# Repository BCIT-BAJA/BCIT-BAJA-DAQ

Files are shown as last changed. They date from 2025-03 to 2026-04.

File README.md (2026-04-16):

# Problem 
During the last BAJA competition,The BAJA team was unable to measure dynamic forces applied onto the suspension of the car. As a result, during the last competition, it bent.



The telemetry system for BCIT-BAJA car, collects strain across suspension components of car to allow BAJA to optimize material and reinforce weak areas of suspension.
As well as collect other data such as linear/angular acceleration.

There consists of 2 parts of this project. 

**PART B** the amplification of the (-15-15mV) analog strain signal to (0-3.0V) which is then routed to

**PART A**, which collects the 8 conditioned analog signals and is transmitted/received over a 915MHz antenna

# MAINBOARD( PART A)

Power supply circuitry


Conditioning of analog signals 


Additional peripherals used


# Amplifier circuit ( PART B) - 


Example of LTSPICE simulation used for amplifier board + signal conditioning



Verified amplifier board working


# Results of real-world appied force vs output voltage 


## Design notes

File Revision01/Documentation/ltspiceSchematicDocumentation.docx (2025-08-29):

# Power supply measurement

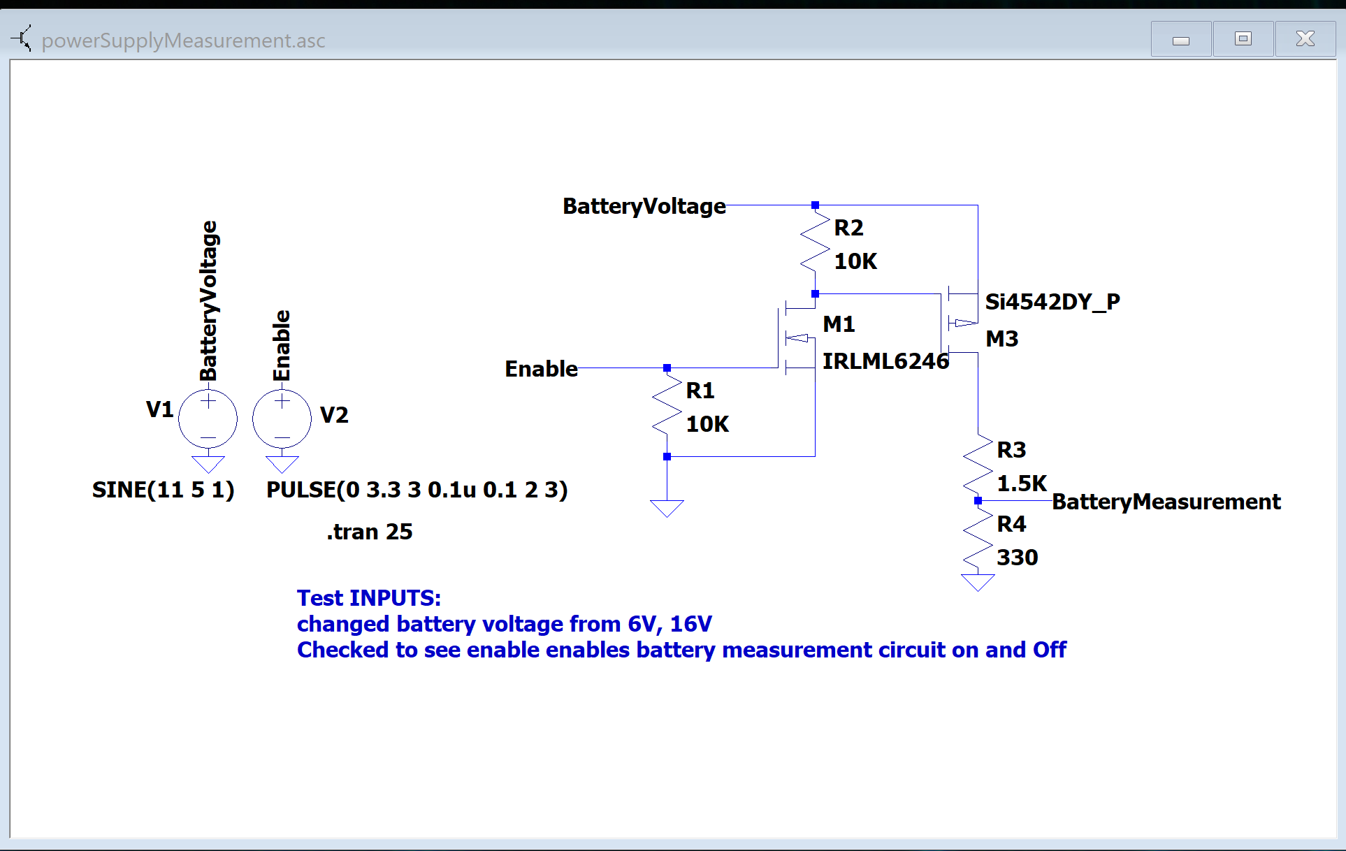
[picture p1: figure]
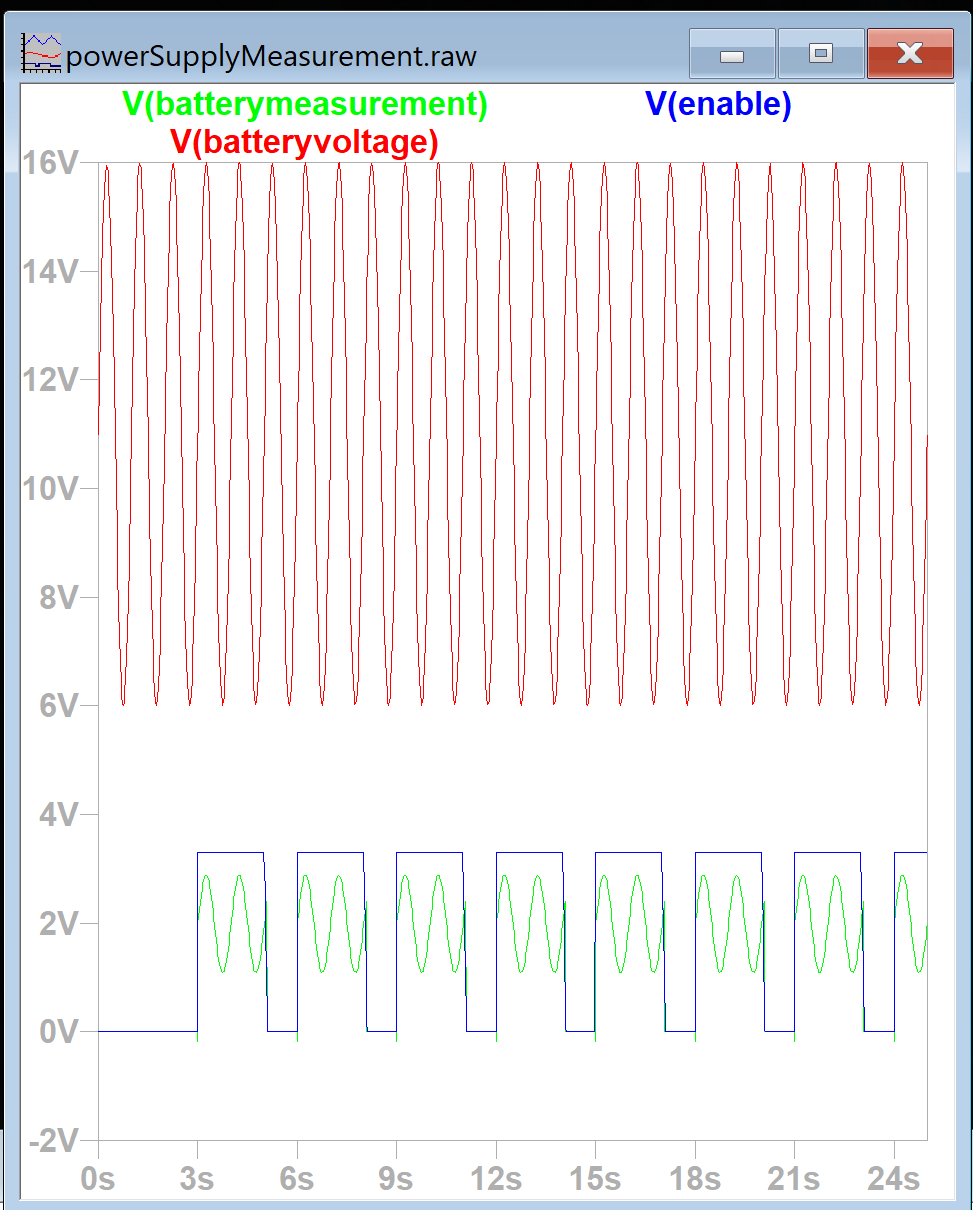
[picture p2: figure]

# StrainGAUGE switching

HIGH C -> LOW EMI, HIGH CURRENT DRAW, DECREASES ACCURACY

CURRENT LIMITING RESISTER -> LOWERS CURRENT, DECREASES ACCURACY

NO/VERY LOW C -> HIGHEST EMI, HIGHEST ACCURACY, lowest current draw.<-- chosen

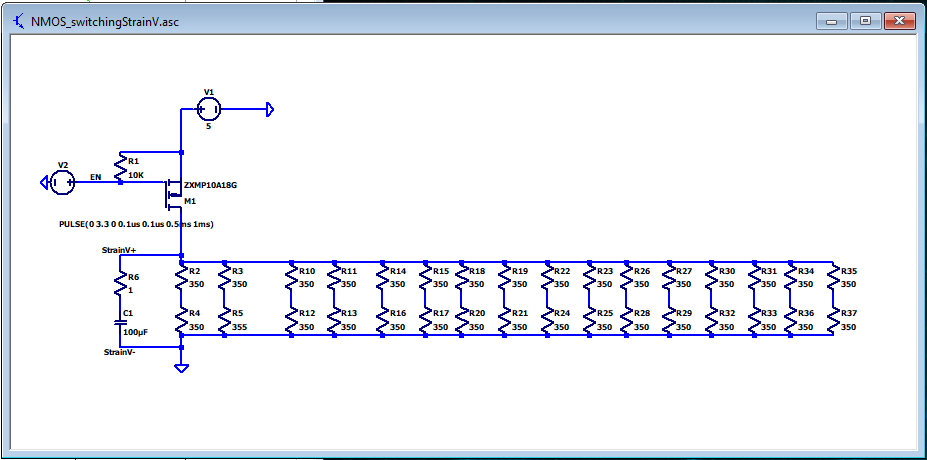
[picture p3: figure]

Figure 1 R =1Ω, C=100uF

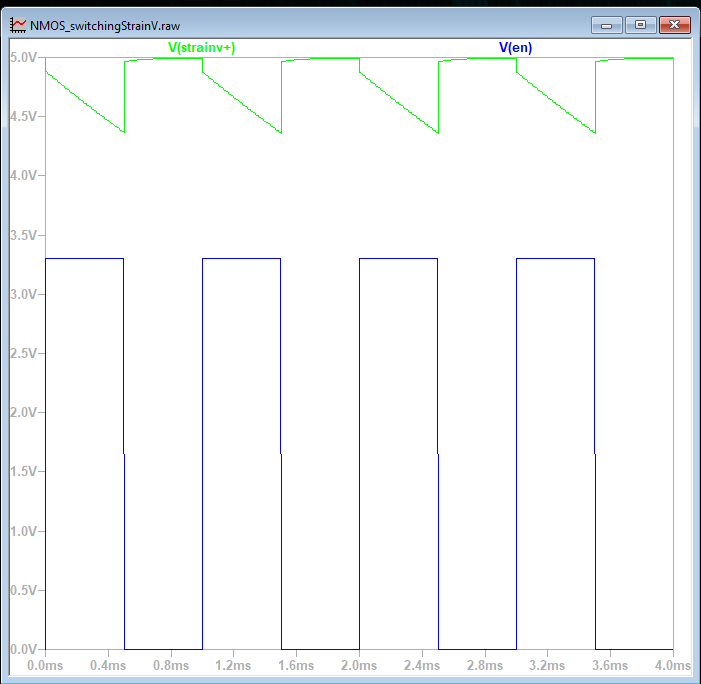
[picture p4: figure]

Figure 2 R =1Ω, C=100uF results

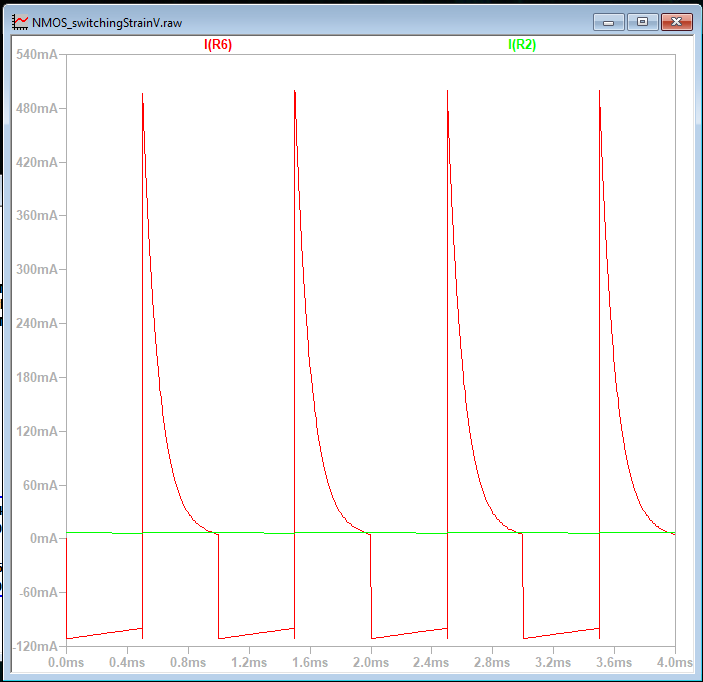
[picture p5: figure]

Figure 3 Current limiting resistor = 1 Ohm, bypass 100uF

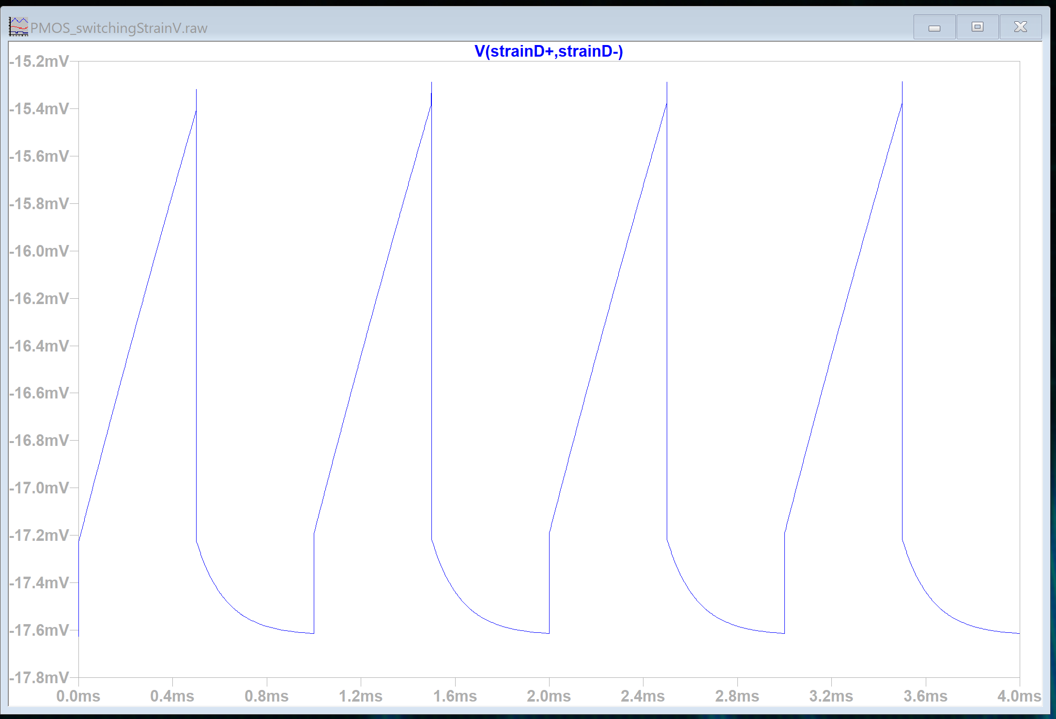
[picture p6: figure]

Figure 4 R =1, C=100uF

# Strain gauge Amplifier

Could not trigger undervoltage conditions on stimulation due to OP-AMP reaching saturation at about 500mV. The stimulated diodes are specced out for worst case condition. Triggering at -182mV, overall, the diodes still protect the ADC at worst-case scenario, however, could not be properly integrated into the stimulation.

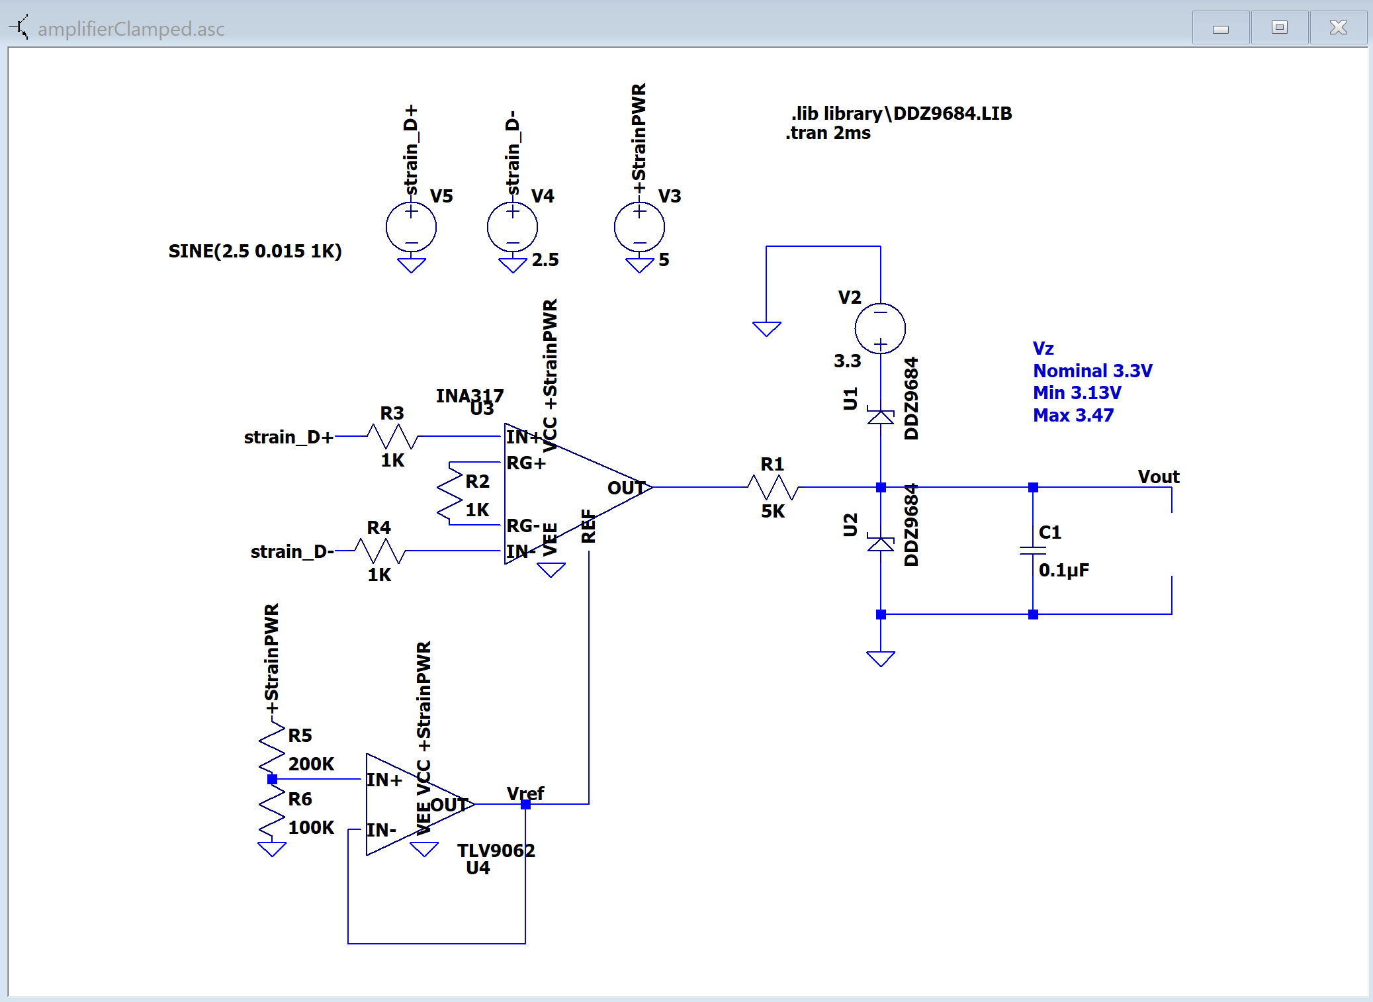
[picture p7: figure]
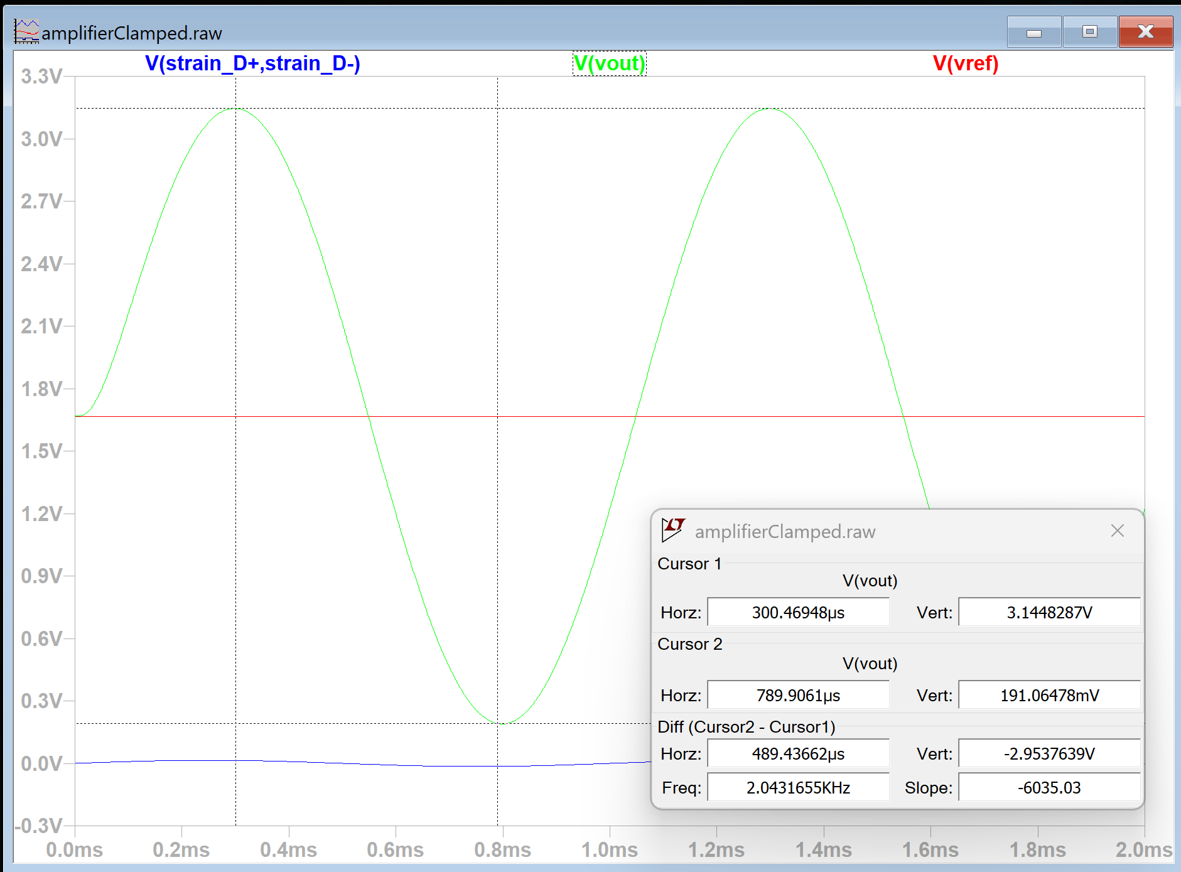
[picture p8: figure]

Diode clamping circuit (*Note, reverse voltage can vary quite a bit as seen by V_z in stimulation schematic)

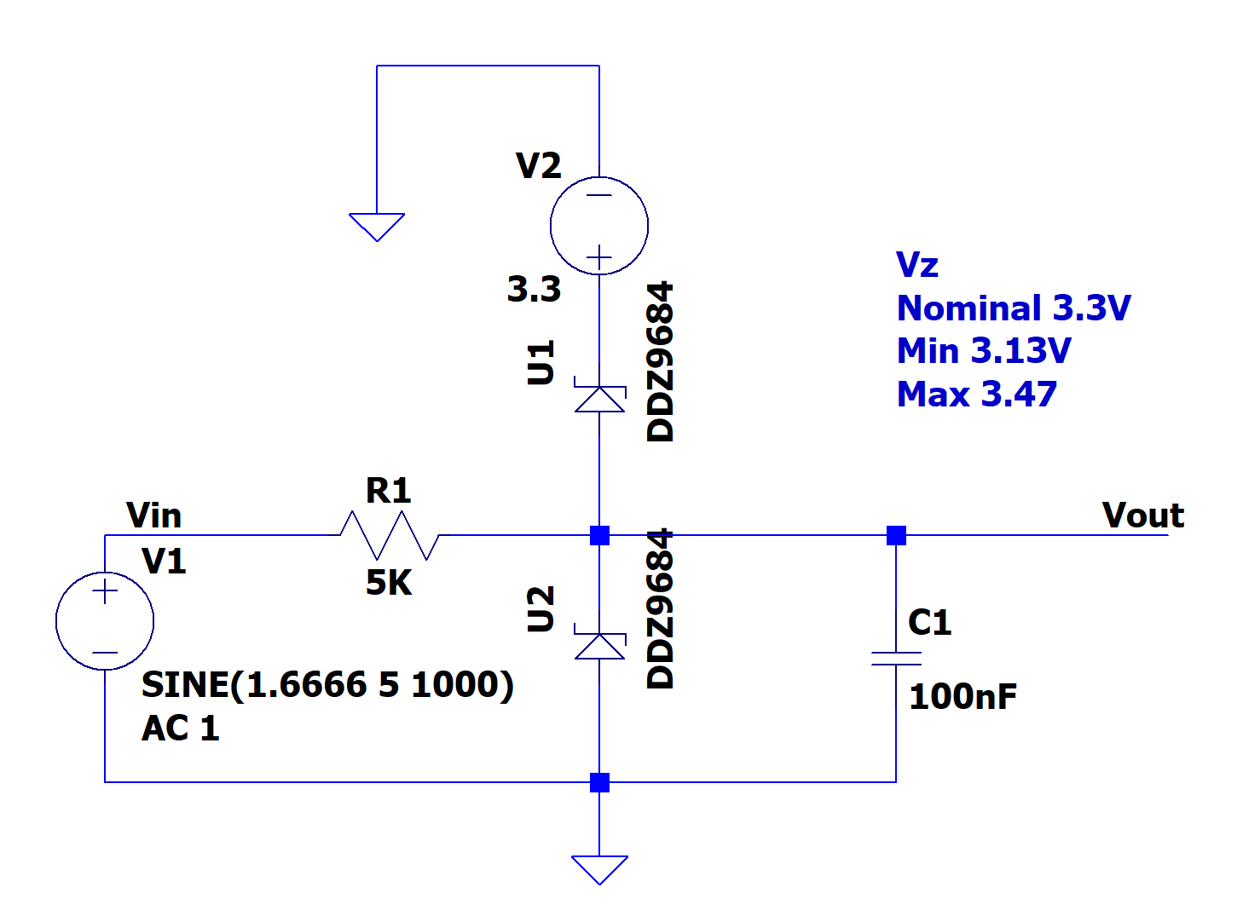
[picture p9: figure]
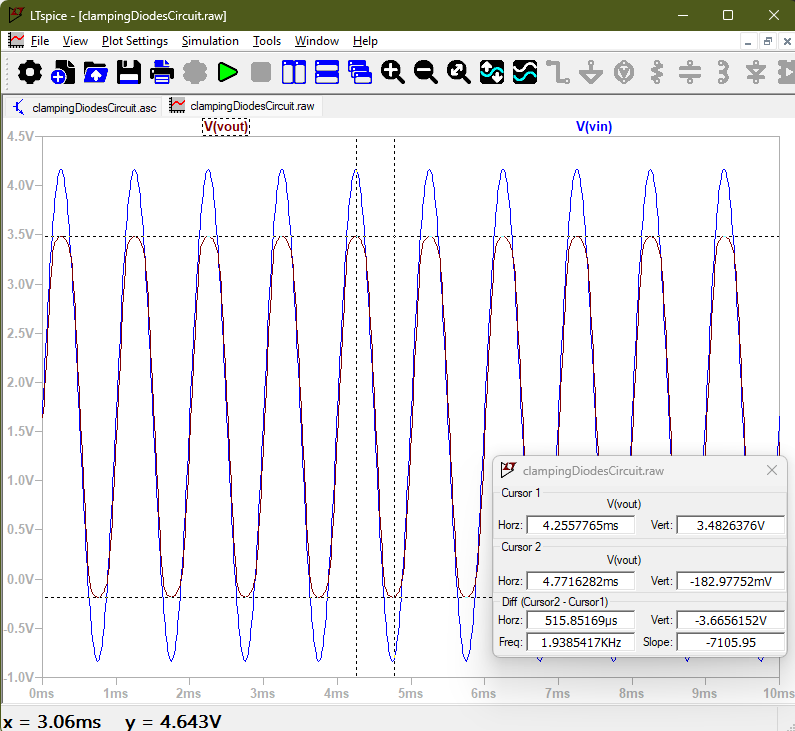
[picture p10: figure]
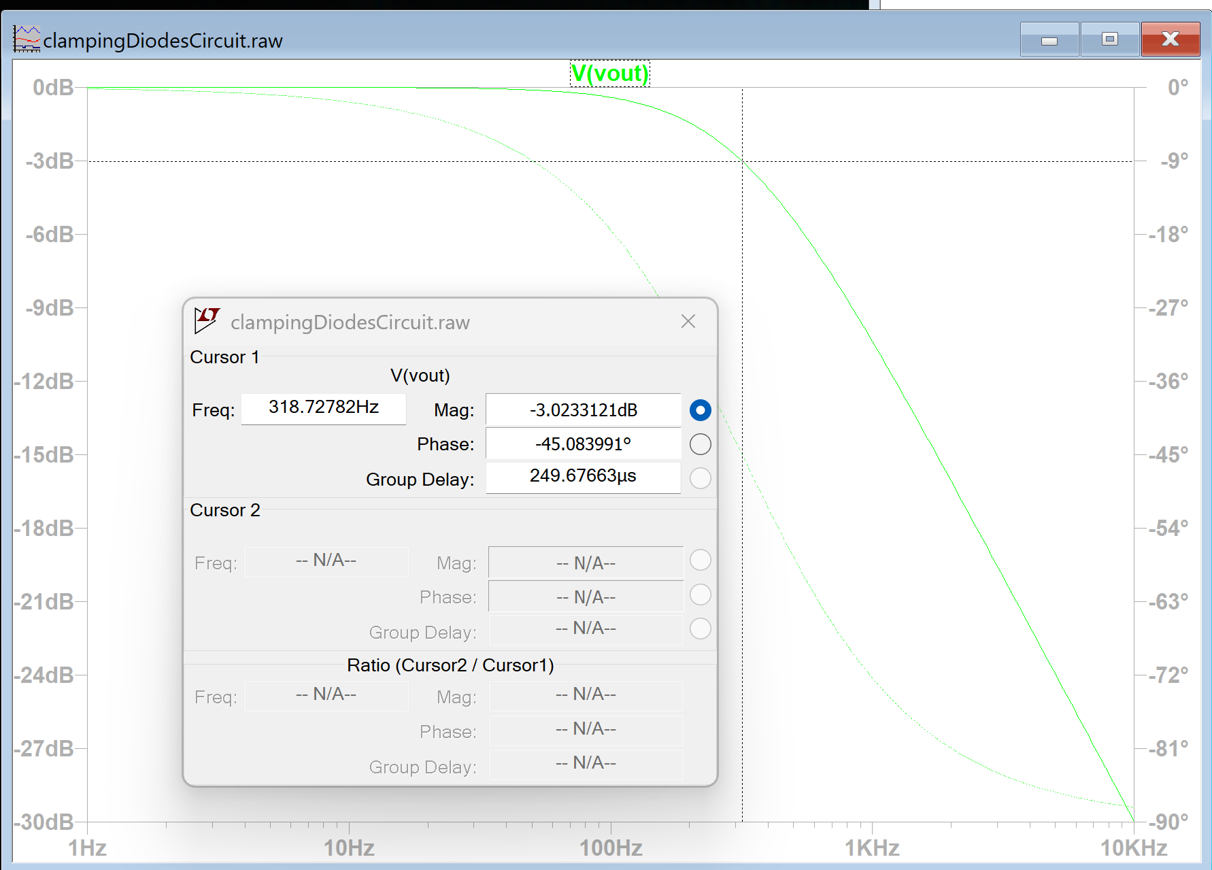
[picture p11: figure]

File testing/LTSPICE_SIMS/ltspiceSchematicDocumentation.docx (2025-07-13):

# Power supply measurement


# StrainGAUGE switching

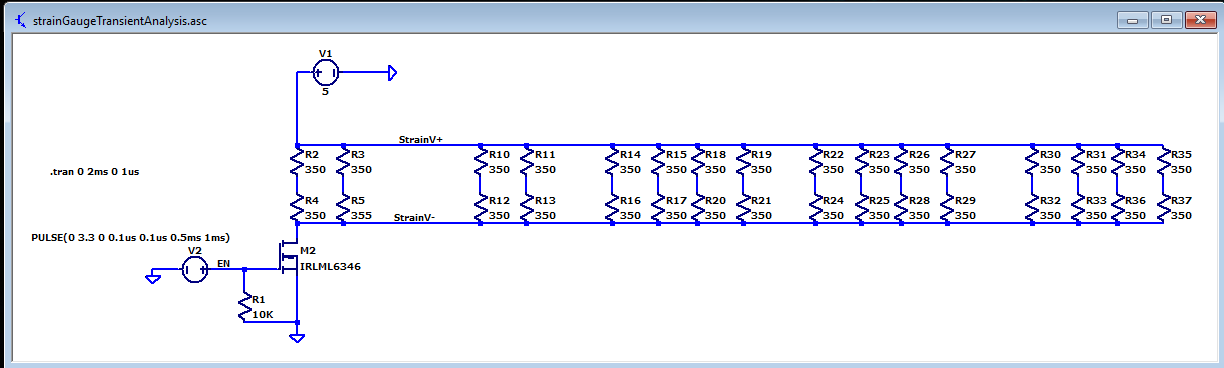
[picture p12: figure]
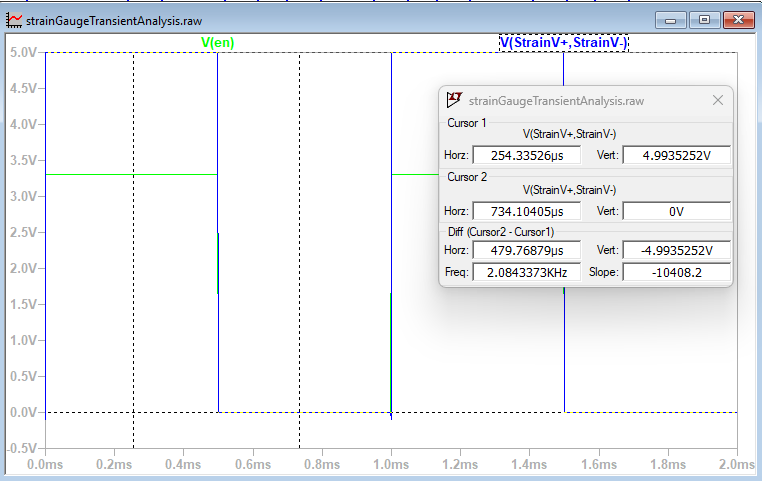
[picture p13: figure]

# Strain gauge Amplifier

I had difficulty combining with the clamping diodes in the next circuit. Wondering if it has to do with the output current of the OP-AMP. Will need to explore this a bit further.

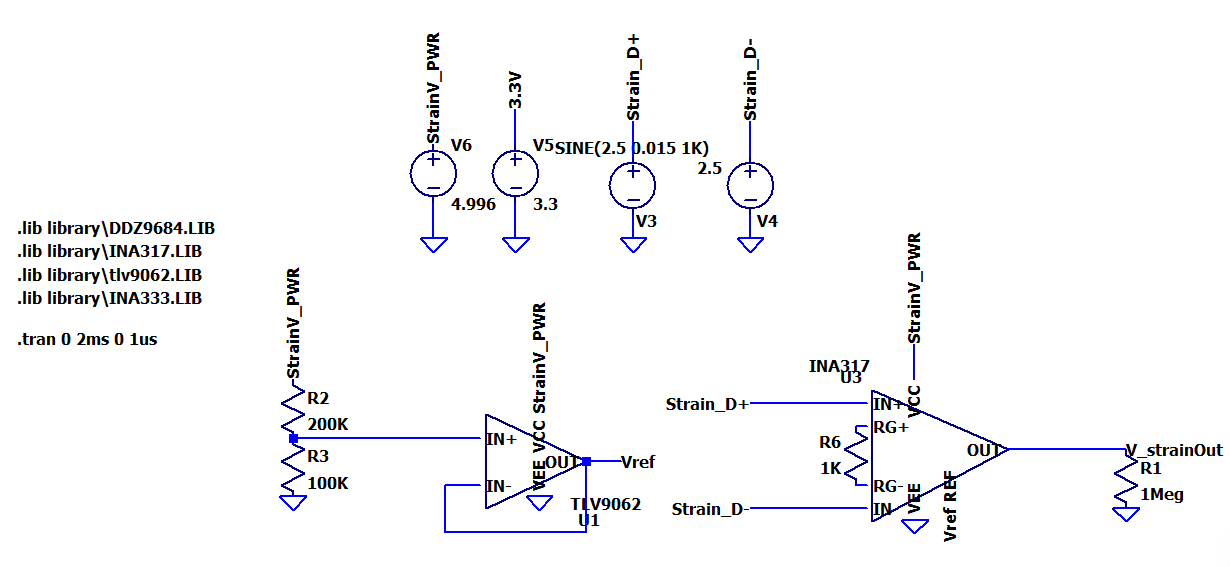
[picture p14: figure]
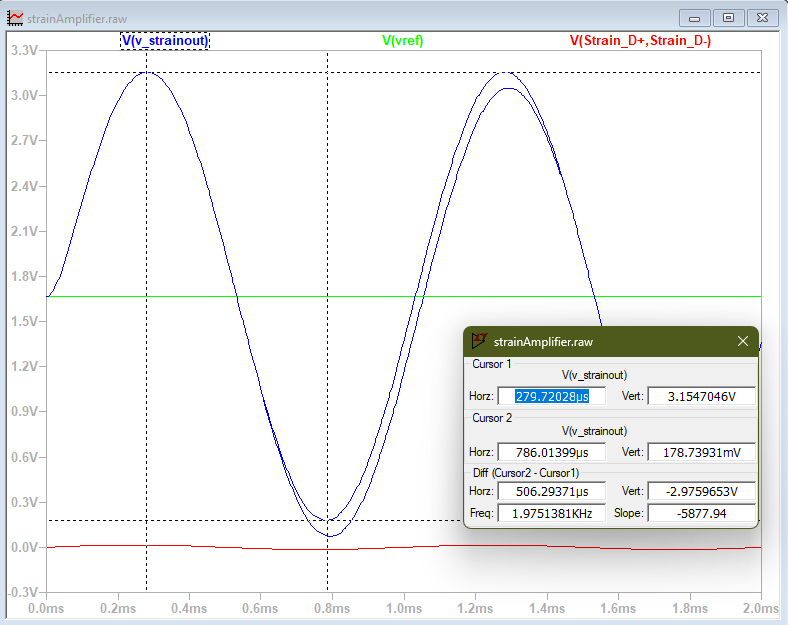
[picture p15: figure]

Diode clamping circuit(*Note, reverse voltage can vary quite a bit as seen by Vz on circuit)

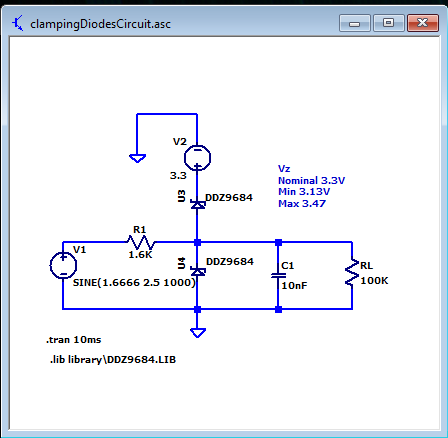
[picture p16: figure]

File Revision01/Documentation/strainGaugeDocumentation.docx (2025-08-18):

PMOS CALCULATIONS

NOTE: Calculations were performed assuming ALL strain gauges are connected. The resistance changes as strain Gauges are disconnected. Though it should be fine if we disconnect some.

For a PMOS

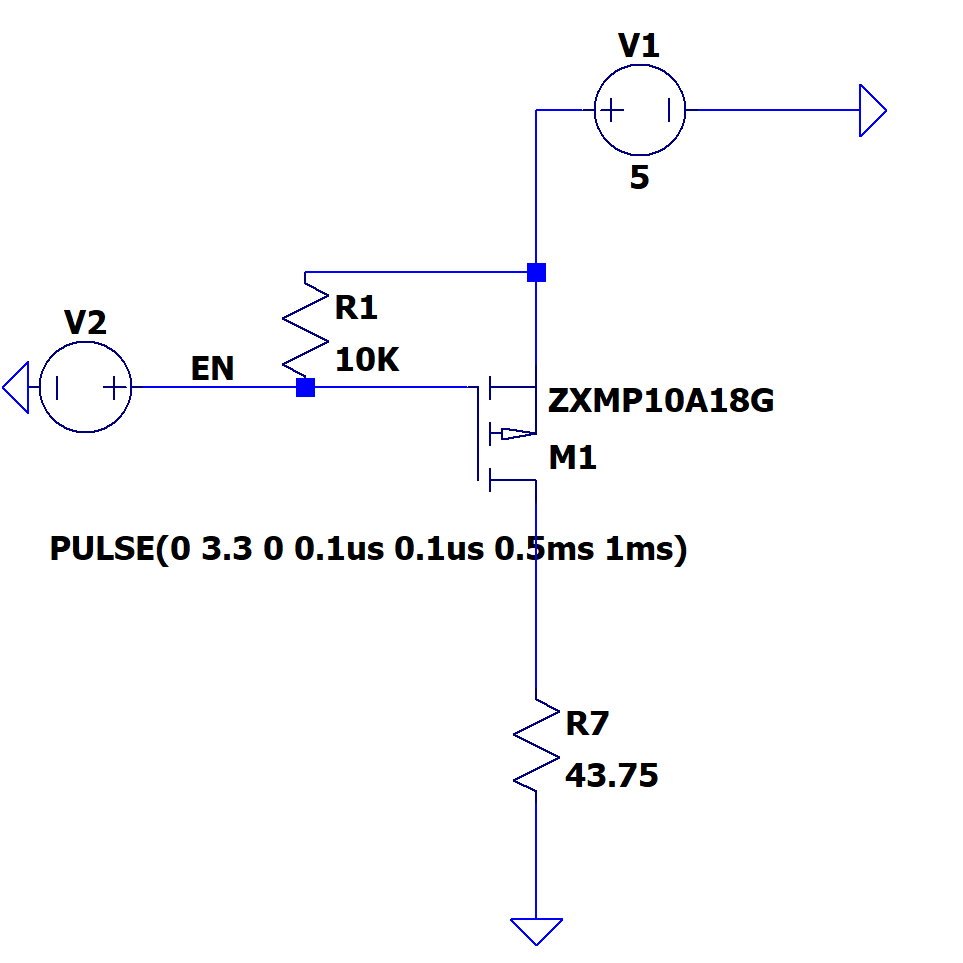
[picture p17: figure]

Figure 1 Similar model was run in stimulation, however not the same as what we choose

CUTOFF REGION: V_(sg) <V_(th_min)

5-3.3<2V

1.7<2V

YES IT can turn off

TRIODE REGION: (FULLY ON)

V_(sg) >V_(th_max)

5 > 4

V_(sd) <V_(sg) -|V_(th_max) |

ASSUME IN TRIODE REGION

Our V_(gs) =-5V when turned on so we can assume R_(ds) ≅1.5Ω

The unknown is V_d

i_d =(5V)/(1.5Ω+43.75Ω)=110mA

V_d =43.75*110mA=4.8125

V_(sd) =5-4.8125=0.1875V

V_(sd) <V_(sg) -|V_(th_max) |

0.1875<5-4

0.1875<1

Very ON!

# Bypass capacitor calculations as PMOS switches 1KHz. Check LTSPICE documentation for more indepth stimulation

I_load = 114mA

Delta T = 0.5ms

Delta V = 0.5V <- just setting it as such

I = C dV/dT

C = I * dT/dV

C = 114mA * 0.5ms / 0.5

= 114 uF ~= 100uF

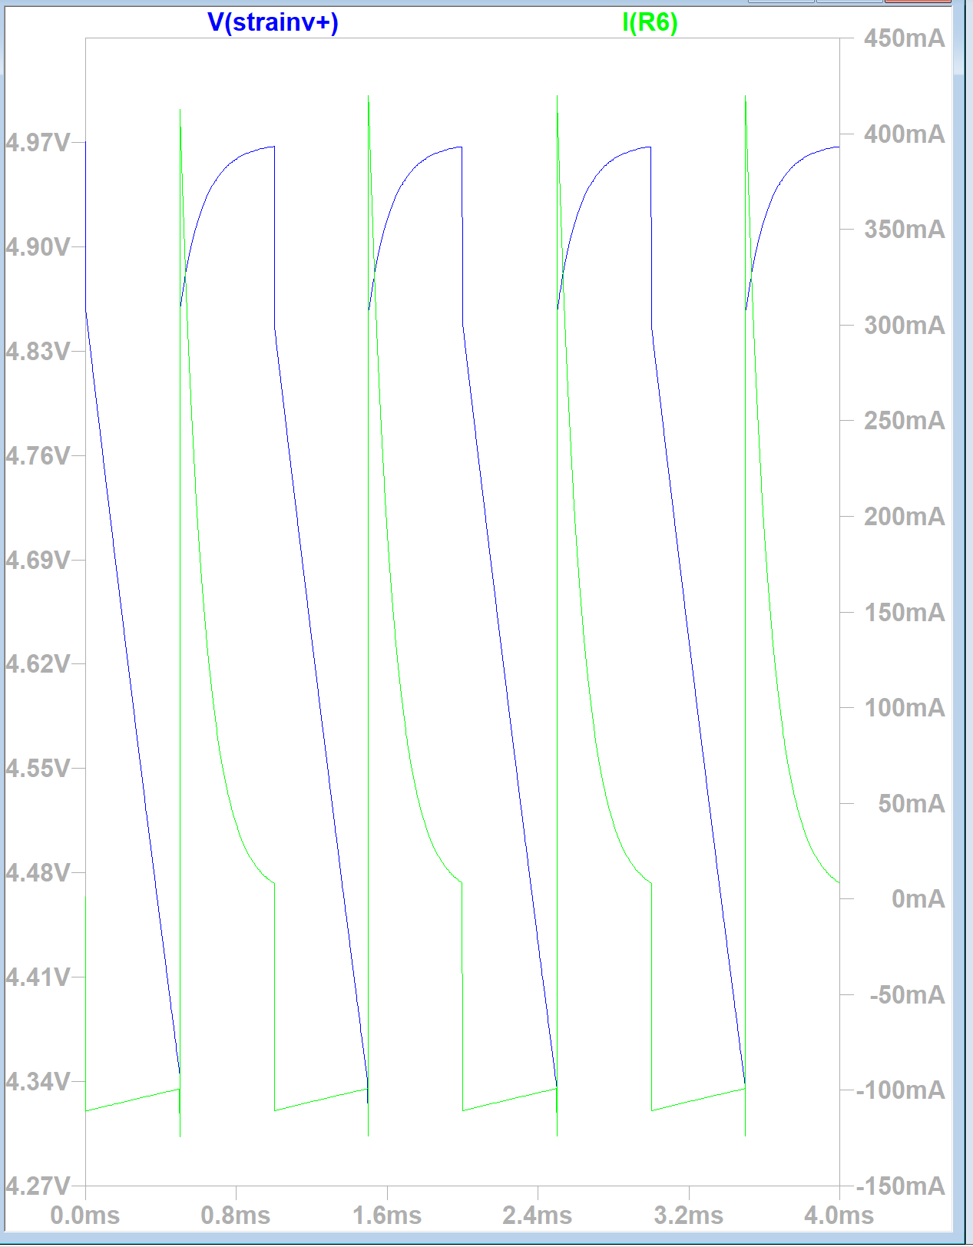
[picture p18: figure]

Figure 2 Assuming C=100uF, ended up not using due to high spike in current

# What happens to differential strain analog signal as 5V rail changes?

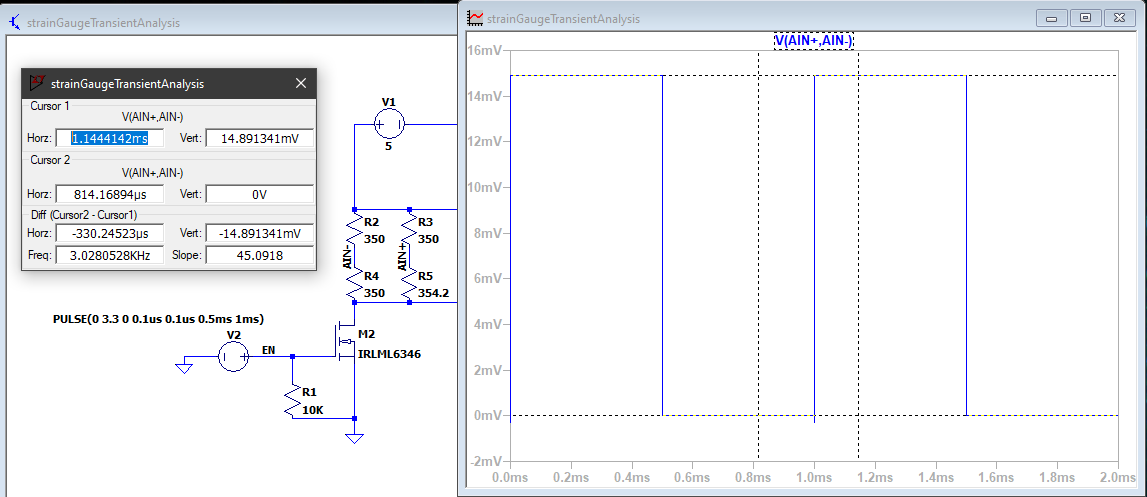
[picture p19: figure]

Figure 3 : 5V rail = 5V, differential signal = 14.89mV

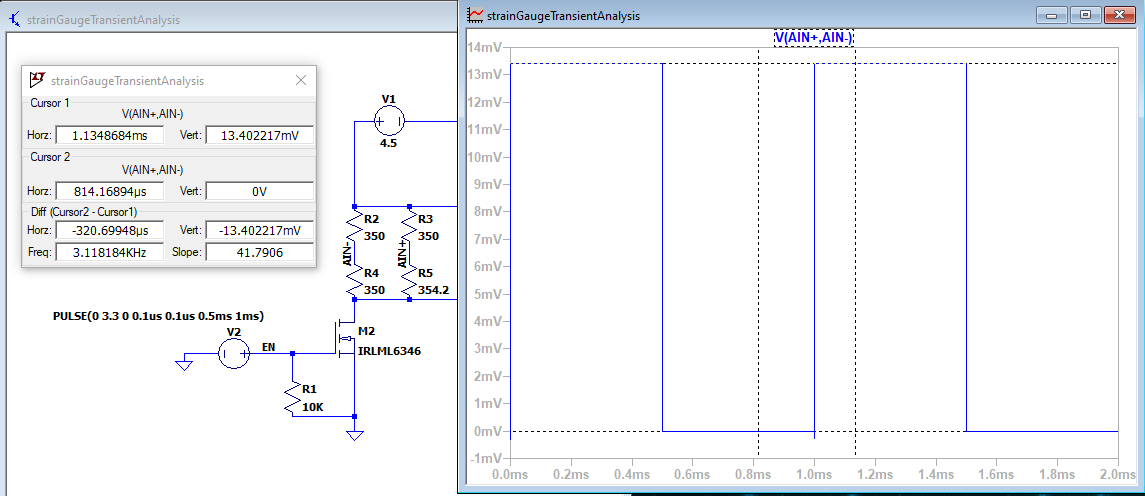
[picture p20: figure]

Figure 4 : 5V rail = 4.5V, differential signal =13.47mV

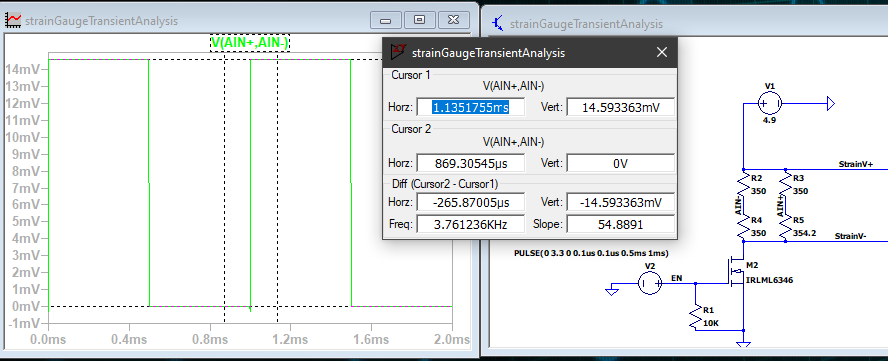
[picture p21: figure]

Figure 5 : 5V rail = 4.9, differential signal =14.59mV

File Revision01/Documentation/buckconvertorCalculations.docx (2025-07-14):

Specifications

1. Verification of PINOUT

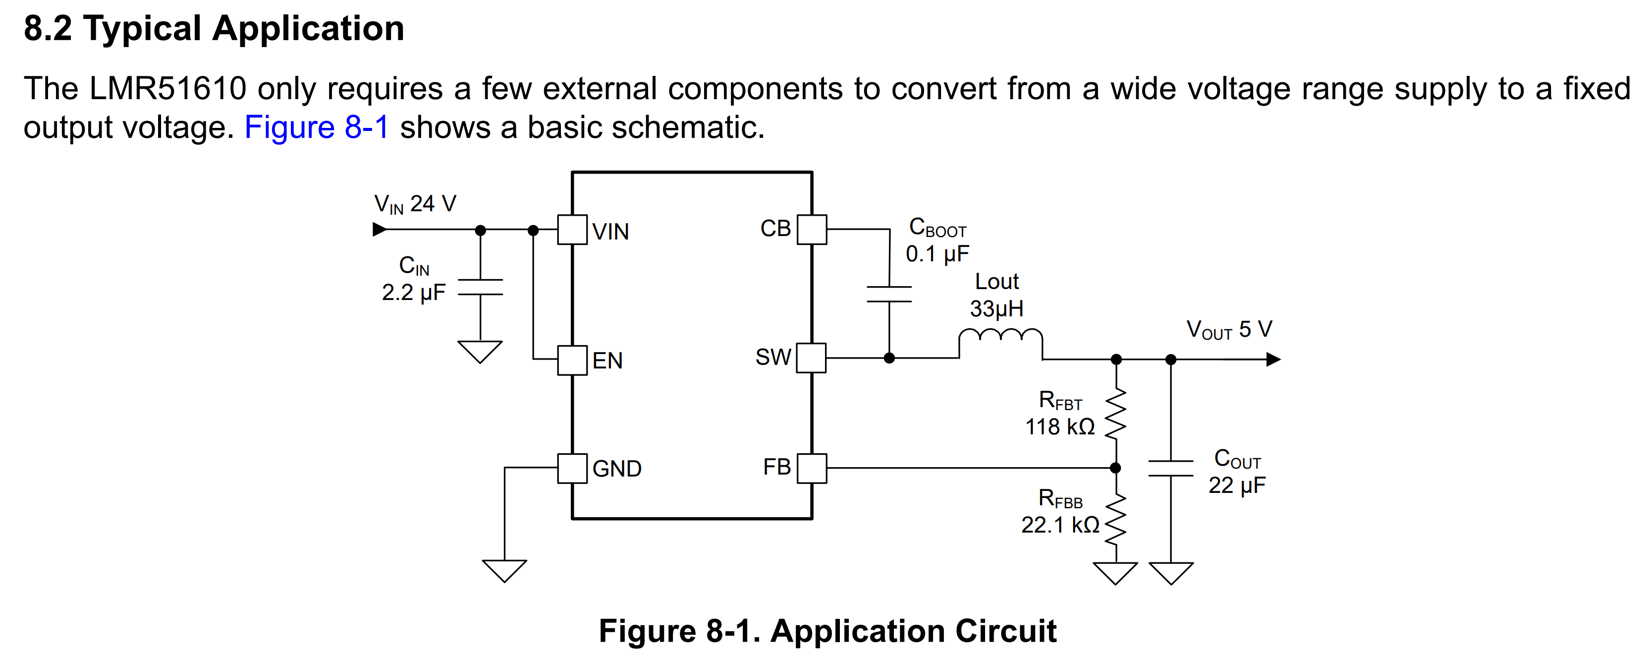
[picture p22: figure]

Design parameters

Parameter | Value
V_(in) | 4.5-16V - Not sure why (8.8V - 15.2V) is on schematic
V_(out) | 7V – must be above 6.5V
i_(out_max) | 250mA – (assuming MOSFET is not switched at 1KHz)
Output overshoot, undershoot | ±5%
Output voltage ripple | ±5%
Operating frequency | 400KHz

2. How do you set the output voltage? (PRIORITY HIGH)

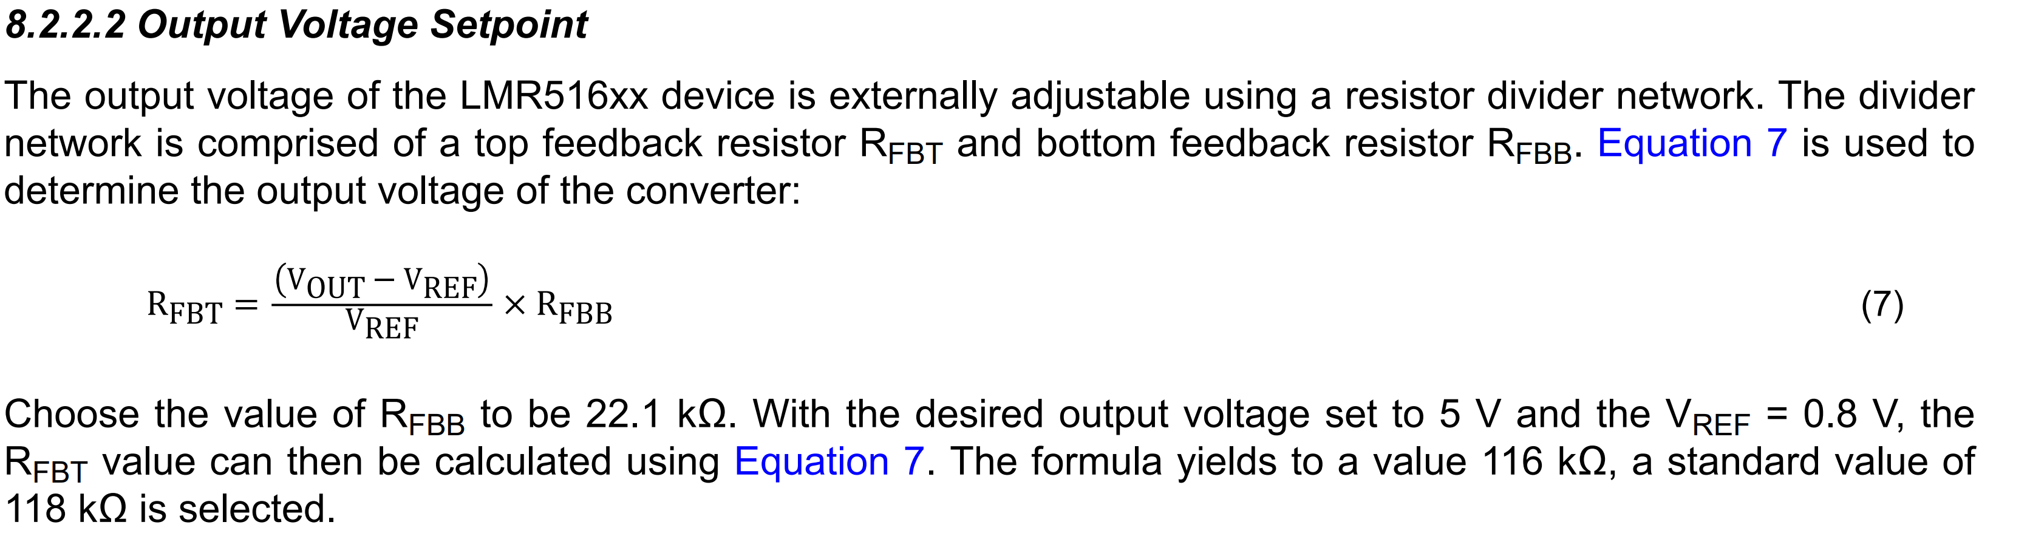
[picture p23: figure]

Defining variables

Choose V_(out) = 7V (Ensure V_(out) is above 6.5V for stable operation of LDO)

V_(ref) = 0.8V (Const)

R_(fbb) = 10K (Randomly chosen)

Plugging that into eq we get

R_(fbt) = (V_(out) - V_(ref) )*(R_(fbb))/(V_(ref))= 77.5K ~= 76.8K

3. How to choose output inductor (PRIORITY MEDIUM)

Overall, I chose parameters that limited EMI, at the cost of being less energy efficient.

K_(IND) is a coefficient that represents the amount of inductor ripple current relative to the maximum output current of the device. K_(IND) must be 0.2-0.6 of maximum IOUT supported by converter.

K_(chosen) = 0.2 – lowest EMI, least energy efficient

f_(sw) =400KHz - lower switching frequency variant chosen for less EMI

V_(in_max) =16V - not sure why 15.2V was chosen

V_(out) =7V±0.5V

I_(out_fla) ~=250mA

Plugging the old parameters in we get

Figure 1 Formula used for inductance

L_(min) =197μH

We chose L =150μH giving us K = 0.26

Now we can calculate the ripple across the input of the inductor using

Figure 2 ripple current(PG 19 datasheet)

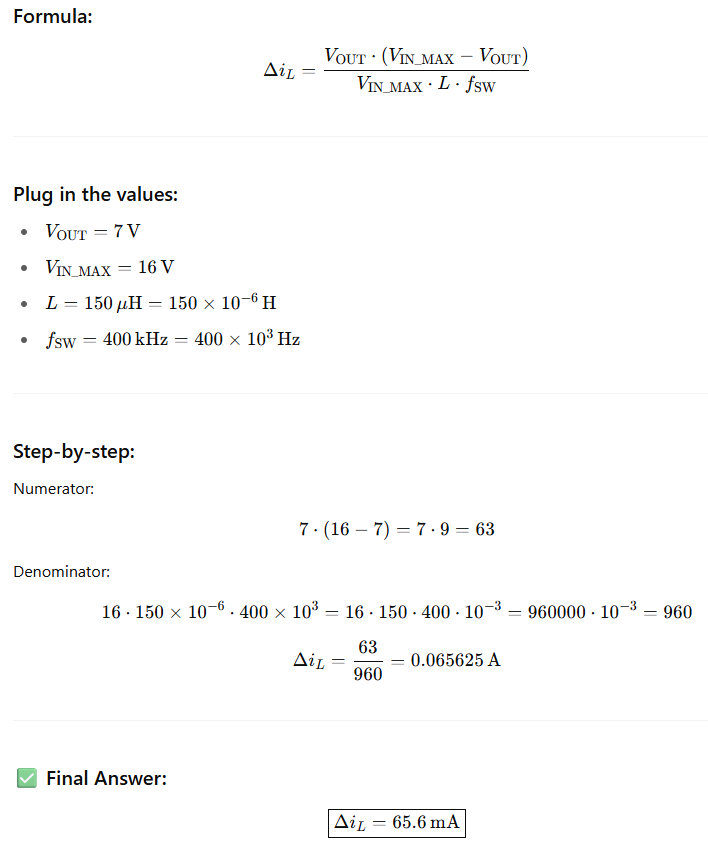
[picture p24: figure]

Note* This inductor has been routed away from analog signals to reduce EMI.

4. Choosing Input capacitors (PRIORITY: LOW)

Followed recommendation using 1uF

5. Choosing output capacitor( PRIORITY: LOWish)

Target ripple is 0.35V

ESR ~= 10m Ω @300KHz

ΔV_(out_esr) =0.66mV

ΔV_(out) _c = 0.93mV


I will have 10uF + 1uF

This one may be better as all wiring has already been created.

Export TPS54202DDCR - 8.5V-16V to 7.00V @ 0.3A

https://webench.ti.com/power-designer/switching-regulator/select

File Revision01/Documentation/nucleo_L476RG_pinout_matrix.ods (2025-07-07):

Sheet: tabula-stm32l476rg(2)
AF15 | Pin | Additional Functions | AF0 | AF1 | AF2 | AF3 | AF4 | AF5 | AF6 | AF7 | AF8 | AF9 | AF10 | AF11 | AF12 | AF13 | AF14 | Pin | Additional Functions | AF0 | AF1 | AF2 | AF3 | AF4 | AF5 | AF6 | AF7 | AF8 | AF9 | AF10 | AF11 | AF12 | AF13 | AF14 | 0
EVENTOUT | PA0 | OPAMP1_VINP/ADC12_IN5/RTC_TAMP2/WKUP1 |  | TIM2_CH1 | TIM5_CH1 | TIM8_ETR |  |  |  | USART2_CTS | UART4_TX |  |  |  |  | SAI1_EXTCLK | TIM2_ETR | PA0 | PA0/OPAMP1_VINP/ADC12_IN5/RTC_TAMP2/WKUP1 | PA0/OPAMP1_VINP/ADC12_IN5/RTC_TAMP2/WKUP1 | PA0/OPAMP1_VINP/ADC12_IN5/RTC_TAMP2/WKUP1/TIM2_CH1 | PA0/OPAMP1_VINP/ADC12_IN5/RTC_TAMP2/WKUP1/TIM2_CH1/TIM5_CH1 | PA0/OPAMP1_VINP/ADC12_IN5/RTC_TAMP2/WKUP1/TIM2_CH1/TIM5_CH1/TIM8_ETR | PA0/OPAMP1_VINP/ADC12_IN5/RTC_TAMP2/WKUP1/TIM2_CH1/TIM5_CH1/TIM8_ETR | PA0/OPAMP1_VINP/ADC12_IN5/RTC_TAMP2/WKUP1/TIM2_CH1/TIM5_CH1/TIM8_ETR | PA0/OPAMP1_VINP/ADC12_IN5/RTC_TAMP2/WKUP1/TIM2_CH1/TIM5_CH1/TIM8_ETR | PA0/OPAMP1_VINP/ADC12_IN5/RTC_TAMP2/WKUP1/TIM2_CH1/TIM5_CH1/TIM8_ETR/USART2_CTS | PA0/OPAMP1_VINP/ADC12_IN5/RTC_TAMP2/WKUP1/TIM2_CH1/TIM5_CH1/TIM8_ETR/USART2_CTS/UART4_TX | PA0/OPAMP1_VINP/ADC12_IN5/RTC_TAMP2/WKUP1/TIM2_CH1/TIM5_CH1/TIM8_ETR/USART2_CTS/UART4_TX | PA0/OPAMP1_VINP/ADC12_IN5/RTC_TAMP2/WKUP1/TIM2_CH1/TIM5_CH1/TIM8_ETR/USART2_CTS/UART4_TX | PA0/OPAMP1_VINP/ADC12_IN5/RTC_TAMP2/WKUP1/TIM2_CH1/TIM5_CH1/TIM8_ETR/USART2_CTS/UART4_TX | PA0/OPAMP1_VINP/ADC12_IN5/RTC_TAMP2/WKUP1/TIM2_CH1/TIM5_CH1/TIM8_ETR/USART2_CTS/UART4_TX | PA0/OPAMP1_VINP/ADC12_IN5/RTC_TAMP2/WKUP1/TIM2_CH1/TIM5_CH1/TIM8_ETR/USART2_CTS/UART4_TX/SAI1_EXTCLK | PA0/OPAMP1_VINP/ADC12_IN5/RTC_TAMP2/WKUP1/TIM2_CH1/TIM5_CH1/TIM8_ETR/USART2_CTS/UART4_TX/SAI1_EXTCLK/TIM2_ETR | PA0/OPAMP1_VINP/ADC12_IN5/RTC_TAMP2/WKUP1/TIM2_CH1/TIM5_CH1/TIM8_ETR/USART2_CTS/UART4_TX/SAI1_EXTCLK/TIM2_ETR
EVENTOUT | PA1 | OPAMP1_VINM/ADC12_IN6 |  | TIM2_CH2 | TIM5_CH2 |  |  |  |  | USART2_RTS_DE | UART4_RX |  |  | LCD_SEG0 |  |  | TIM15_CH1N | PA1 | PA1/OPAMP1_VINM/ADC12_IN6 | PA1/OPAMP1_VINM/ADC12_IN6 | PA1/OPAMP1_VINM/ADC12_IN6/TIM2_CH2 | PA1/OPAMP1_VINM/ADC12_IN6/TIM2_CH2/TIM5_CH2 | PA1/OPAMP1_VINM/ADC12_IN6/TIM2_CH2/TIM5_CH2 | PA1/OPAMP1_VINM/ADC12_IN6/TIM2_CH2/TIM5_CH2 | PA1/OPAMP1_VINM/ADC12_IN6/TIM2_CH2/TIM5_CH2 | PA1/OPAMP1_VINM/ADC12_IN6/TIM2_CH2/TIM5_CH2 | PA1/OPAMP1_VINM/ADC12_IN6/TIM2_CH2/TIM5_CH2/USART2_RTS_DE | PA1/OPAMP1_VINM/ADC12_IN6/TIM2_CH2/TIM5_CH2/USART2_RTS_DE/UART4_RX | PA1/OPAMP1_VINM/ADC12_IN6/TIM2_CH2/TIM5_CH2/USART2_RTS_DE/UART4_RX | PA1/OPAMP1_VINM/ADC12_IN6/TIM2_CH2/TIM5_CH2/USART2_RTS_DE/UART4_RX | PA1/OPAMP1_VINM/ADC12_IN6/TIM2_CH2/TIM5_CH2/USART2_RTS_DE/UART4_RX/LCD_SEG0 | PA1/OPAMP1_VINM/ADC12_IN6/TIM2_CH2/TIM5_CH2/USART2_RTS_DE/UART4_RX/LCD_SEG0 | PA1/OPAMP1_VINM/ADC12_IN6/TIM2_CH2/TIM5_CH2/USART2_RTS_DE/UART4_RX/LCD_SEG0 | PA1/OPAMP1_VINM/ADC12_IN6/TIM2_CH2/TIM5_CH2/USART2_RTS_DE/UART4_RX/LCD_SEG0/TIM15_CH1N | PA1/OPAMP1_VINM/ADC12_IN6/TIM2_CH2/TIM5_CH2/USART2_RTS_DE/UART4_RX/LCD_SEG0/TIM15_CH1N
EVENTOUT | PA2 | ADC12_IN7/WKUP4/LSCO |  | TIM2_CH3 | TIM5_CH3 |  |  |  |  | USART2_TX |  |  |  | LCD_SEG1 |  | SAI2_EXTCLK | TIM15_CH1 | PA2 | PA2/ADC12_IN7/WKUP4/LSCO | PA2/ADC12_IN7/WKUP4/LSCO | PA2/ADC12_IN7/WKUP4/LSCO/TIM2_CH3 | PA2/ADC12_IN7/WKUP4/LSCO/TIM2_CH3/TIM5_CH3 | PA2/ADC12_IN7/WKUP4/LSCO/TIM2_CH3/TIM5_CH3 | PA2/ADC12_IN7/WKUP4/LSCO/TIM2_CH3/TIM5_CH3 | PA2/ADC12_IN7/WKUP4/LSCO/TIM2_CH3/TIM5_CH3 | PA2/ADC12_IN7/WKUP4/LSCO/TIM2_CH3/TIM5_CH3 | PA2/ADC12_IN7/WKUP4/LSCO/TIM2_CH3/TIM5_CH3/USART2_TX | PA2/ADC12_IN7/WKUP4/LSCO/TIM2_CH3/TIM5_CH3/USART2_TX | PA2/ADC12_IN7/WKUP4/LSCO/TIM2_CH3/TIM5_CH3/USART2_TX | PA2/ADC12_IN7/WKUP4/LSCO/TIM2_CH3/TIM5_CH3/USART2_TX | PA2/ADC12_IN7/WKUP4/LSCO/TIM2_CH3/TIM5_CH3/USART2_TX/LCD_SEG1 | PA2/ADC12_IN7/WKUP4/LSCO/TIM2_CH3/TIM5_CH3/USART2_TX/LCD_SEG1 | PA2/ADC12_IN7/WKUP4/LSCO/TIM2_CH3/TIM5_CH3/USART2_TX/LCD_SEG1/SAI2_EXTCLK | PA2/ADC12_IN7/WKUP4/LSCO/TIM2_CH3/TIM5_CH3/USART2_TX/LCD_SEG1/SAI2_EXTCLK/TIM15_CH1 | PA2/ADC12_IN7/WKUP4/LSCO/TIM2_CH3/TIM5_CH3/USART2_TX/LCD_SEG1/SAI2_EXTCLK/TIM15_CH1
EVENTOUT | PA3 | OPAMP1_VOUT/ADC12_IN8 |  | TIM2_CH4 | TIM5_CH4 |  |  |  |  | USART2_RX |  |  |  | LCD_SEG2 |  |  | TIM15_CH2 | PA3 | PA3/OPAMP1_VOUT/ADC12_IN8 | PA3/OPAMP1_VOUT/ADC12_IN8 | PA3/OPAMP1_VOUT/ADC12_IN8/TIM2_CH4 | PA3/OPAMP1_VOUT/ADC12_IN8/TIM2_CH4/TIM5_CH4 | PA3/OPAMP1_VOUT/ADC12_IN8/TIM2_CH4/TIM5_CH4 | PA3/OPAMP1_VOUT/ADC12_IN8/TIM2_CH4/TIM5_CH4 | PA3/OPAMP1_VOUT/ADC12_IN8/TIM2_CH4/TIM5_CH4 | PA3/OPAMP1_VOUT/ADC12_IN8/TIM2_CH4/TIM5_CH4 | PA3/OPAMP1_VOUT/ADC12_IN8/TIM2_CH4/TIM5_CH4/USART2_RX | PA3/OPAMP1_VOUT/ADC12_IN8/TIM2_CH4/TIM5_CH4/USART2_RX | PA3/OPAMP1_VOUT/ADC12_IN8/TIM2_CH4/TIM5_CH4/USART2_RX | PA3/OPAMP1_VOUT/ADC12_IN8/TIM2_CH4/TIM5_CH4/USART2_RX | PA3/OPAMP1_VOUT/ADC12_IN8/TIM2_CH4/TIM5_CH4/USART2_RX/LCD_SEG2 | PA3/OPAMP1_VOUT/ADC12_IN8/TIM2_CH4/TIM5_CH4/USART2_RX/LCD_SEG2 | PA3/OPAMP1_VOUT/ADC12_IN8/TIM2_CH4/TIM5_CH4/USART2_RX/LCD_SEG2 | PA3/OPAMP1_VOUT/ADC12_IN8/TIM2_CH4/TIM5_CH4/USART2_RX/LCD_SEG2/TIM15_CH2 | PA3/OPAMP1_VOUT/ADC12_IN8/TIM2_CH4/TIM5_CH4/USART2_RX/LCD_SEG2/TIM15_CH2
EVENTOUT | PA4 | ADC12_IN9/DAC1_OUT1 |  |  |  |  |  | SPI1_NSS | SPI3_NSS | USART2_CK |  |  |  |  |  | SAI1_FS_B | LPTIM2_OUT | PA4 | PA4/ADC12_IN9/DAC1_OUT1 | PA4/ADC12_IN9/DAC1_OUT1 | PA4/ADC12_IN9/DAC1_OUT1 | PA4/ADC12_IN9/DAC1_OUT1 | PA4/ADC12_IN9/DAC1_OUT1 | PA4/ADC12_IN9/DAC1_OUT1 | PA4/ADC12_IN9/DAC1_OUT1/SPI1_NSS | PA4/ADC12_IN9/DAC1_OUT1/SPI1_NSS/SPI3_NSS | PA4/ADC12_IN9/DAC1_OUT1/SPI1_NSS/SPI3_NSS/USART2_CK | PA4/ADC12_IN9/DAC1_OUT1/SPI1_NSS/SPI3_NSS/USART2_CK | PA4/ADC12_IN9/DAC1_OUT1/SPI1_NSS/SPI3_NSS/USART2_CK | PA4/ADC12_IN9/DAC1_OUT1/SPI1_NSS/SPI3_NSS/USART2_CK | PA4/ADC12_IN9/DAC1_OUT1/SPI1_NSS/SPI3_NSS/USART2_CK | PA4/ADC12_IN9/DAC1_OUT1/SPI1_NSS/SPI3_NSS/USART2_CK | PA4/ADC12_IN9/DAC1_OUT1/SPI1_NSS/SPI3_NSS/USART2_CK/SAI1_FS_B | PA4/ADC12_IN9/DAC1_OUT1/SPI1_NSS/SPI3_NSS/USART2_CK/SAI1_FS_B/LPTIM2_OUT | PA4/ADC12_IN9/DAC1_OUT1/SPI1_NSS/SPI3_NSS/USART2_CK/SAI1_FS_B/LPTIM2_OUT
EVENTOUT | PA5 | ADC12_IN10/DAC1_OUT2 |  | TIM2_CH1 | TIM2_ETR | TIM8_CH1N |  | SPI1_SCK |  |  |  |  |  |  |  |  | LPTIM2_ETR | PA5 | PA5/ADC12_IN10/DAC1_OUT2 | PA5/ADC12_IN10/DAC1_OUT2 | PA5/ADC12_IN10/DAC1_OUT2/TIM2_CH1 | PA5/ADC12_IN10/DAC1_OUT2/TIM2_CH1/TIM2_ETR | PA5/ADC12_IN10/DAC1_OUT2/TIM2_CH1/TIM2_ETR/TIM8_CH1N | PA5/ADC12_IN10/DAC1_OUT2/TIM2_CH1/TIM2_ETR/TIM8_CH1N | PA5/ADC12_IN10/DAC1_OUT2/TIM2_CH1/TIM2_ETR/TIM8_CH1N/SPI1_SCK | PA5/ADC12_IN10/DAC1_OUT2/TIM2_CH1/TIM2_ETR/TIM8_CH1N/SPI1_SCK | PA5/ADC12_IN10/DAC1_OUT2/TIM2_CH1/TIM2_ETR/TIM8_CH1N/SPI1_SCK | PA5/ADC12_IN10/DAC1_OUT2/TIM2_CH1/TIM2_ETR/TIM8_CH1N/SPI1_SCK | PA5/ADC12_IN10/DAC1_OUT2/TIM2_CH1/TIM2_ETR/TIM8_CH1N/SPI1_SCK | PA5/ADC12_IN10/DAC1_OUT2/TIM2_CH1/TIM2_ETR/TIM8_CH1N/SPI1_SCK | PA5/ADC12_IN10/DAC1_OUT2/TIM2_CH1/TIM2_ETR/TIM8_CH1N/SPI1_SCK | PA5/ADC12_IN10/DAC1_OUT2/TIM2_CH1/TIM2_ETR/TIM8_CH1N/SPI1_SCK | PA5/ADC12_IN10/DAC1_OUT2/TIM2_CH1/TIM2_ETR/TIM8_CH1N/SPI1_SCK | PA5/ADC12_IN10/DAC1_OUT2/TIM2_CH1/TIM2_ETR/TIM8_CH1N/SPI1_SCK/LPTIM2_ETR | PA5/ADC12_IN10/DAC1_OUT2/TIM2_CH1/TIM2_ETR/TIM8_CH1N/SPI1_SCK/LPTIM2_ETR
EVENTOUT | PA6 | OPAMP2_VINP/ADC12_IN11 |  | TIM1_BKIN | TIM3_CH1 | TIM8_BKIN |  | SPI1_MISO |  | USART3_CTS |  |  | QUADSPI_BK1_IO3 | LCD_SEG3 | TIM1_BKIN_COMP2 | TIM8_BKIN_COMP2 | TIM16_CH1 | PA6 | PA6/OPAMP2_VINP/ADC12_IN11 | PA6/OPAMP2_VINP/ADC12_IN11 | PA6/OPAMP2_VINP/ADC12_IN11/TIM1_BKIN | PA6/OPAMP2_VINP/ADC12_IN11/TIM1_BKIN/TIM3_CH1 | PA6/OPAMP2_VINP/ADC12_IN11/TIM1_BKIN/TIM3_CH1/TIM8_BKIN | PA6/OPAMP2_VINP/ADC12_IN11/TIM1_BKIN/TIM3_CH1/TIM8_BKIN | PA6/OPAMP2_VINP/ADC12_IN11/TIM1_BKIN/TIM3_CH1/TIM8_BKIN/SPI1_MISO | PA6/OPAMP2_VINP/ADC12_IN11/TIM1_BKIN/TIM3_CH1/TIM8_BKIN/SPI1_MISO | PA6/OPAMP2_VINP/ADC12_IN11/TIM1_BKIN/TIM3_CH1/TIM8_BKIN/SPI1_MISO/USART3_CTS | PA6/OPAMP2_VINP/ADC12_IN11/TIM1_BKIN/TIM3_CH1/TIM8_BKIN/SPI1_MISO/USART3_CTS | PA6/OPAMP2_VINP/ADC12_IN11/TIM1_BKIN/TIM3_CH1/TIM8_BKIN/SPI1_MISO/USART3_CTS | PA6/OPAMP2_VINP/ADC12_IN11/TIM1_BKIN/TIM3_CH1/TIM8_BKIN/SPI1_MISO/USART3_CTS/QUADSPI_BK1_IO3 | PA6/OPAMP2_VINP/ADC12_IN11/TIM1_BKIN/TIM3_CH1/TIM8_BKIN/SPI1_MISO/USART3_CTS/QUADSPI_BK1_IO3/LCD_SEG3 | PA6/OPAMP2_VINP/ADC12_IN11/TIM1_BKIN/TIM3_CH1/TIM8_BKIN/SPI1_MISO/USART3_CTS/QUADSPI_BK1_IO3/LCD_SEG3/TIM1_BKIN_COMP2 | PA6/OPAMP2_VINP/ADC12_IN11/TIM1_BKIN/TIM3_CH1/TIM8_BKIN/SPI1_MISO/USART3_CTS/QUADSPI_BK1_IO3/LCD_SEG3/TIM1_BKIN_COMP2/TIM8_BKIN_COMP2 | PA6/OPAMP2_VINP/ADC12_IN11/TIM1_BKIN/TIM3_CH1/TIM8_BKIN/SPI1_MISO/USART3_CTS/QUADSPI_BK1_IO3/LCD_SEG3/TIM1_BKIN_COMP2/TIM8_BKIN_COMP2/TIM16_CH1 | PA6/OPAMP2_VINP/ADC12_IN11/TIM1_BKIN/TIM3_CH1/TIM8_BKIN/SPI1_MISO/USART3_CTS/QUADSPI_BK1_IO3/LCD_SEG3/TIM1_BKIN_COMP2/TIM8_BKIN_COMP2/TIM16_CH1
EVENTOUT | PA7 | OPAMP2_VINM/ADC12_IN12 |  | TIM1_CH1N | TIM3_CH2 | TIM8_CH1N |  | SPI1_MOSI |  |  |  |  | QUADSPI_BK1_IO2 | LCD_SEG4 |  |  | TIM17_CH1 | PA7 | PA7/OPAMP2_VINM/ADC12_IN12 | PA7/OPAMP2_VINM/ADC12_IN12 | PA7/OPAMP2_VINM/ADC12_IN12/TIM1_CH1N | PA7/OPAMP2_VINM/ADC12_IN12/TIM1_CH1N/TIM3_CH2 | PA7/OPAMP2_VINM/ADC12_IN12/TIM1_CH1N/TIM3_CH2/TIM8_CH1N | PA7/OPAMP2_VINM/ADC12_IN12/TIM1_CH1N/TIM3_CH2/TIM8_CH1N | PA7/OPAMP2_VINM/ADC12_IN12/TIM1_CH1N/TIM3_CH2/TIM8_CH1N/SPI1_MOSI | PA7/OPAMP2_VINM/ADC12_IN12/TIM1_CH1N/TIM3_CH2/TIM8_CH1N/SPI1_MOSI | PA7/OPAMP2_VINM/ADC12_IN12/TIM1_CH1N/TIM3_CH2/TIM8_CH1N/SPI1_MOSI | PA7/OPAMP2_VINM/ADC12_IN12/TIM1_CH1N/TIM3_CH2/TIM8_CH1N/SPI1_MOSI | PA7/OPAMP2_VINM/ADC12_IN12/TIM1_CH1N/TIM3_CH2/TIM8_CH1N/SPI1_MOSI | PA7/OPAMP2_VINM/ADC12_IN12/TIM1_CH1N/TIM3_CH2/TIM8_CH1N/SPI1_MOSI/QUADSPI_BK1_IO2 | PA7/OPAMP2_VINM/ADC12_IN12/TIM1_CH1N/TIM3_CH2/TIM8_CH1N/SPI1_MOSI/QUADSPI_BK1_IO2/LCD_SEG4 | PA7/OPAMP2_VINM/ADC12_IN12/TIM1_CH1N/TIM3_CH2/TIM8_CH1N/SPI1_MOSI/QUADSPI_BK1_IO2/LCD_SEG4 | PA7/OPAMP2_VINM/ADC12_IN12/TIM1_CH1N/TIM3_CH2/TIM8_CH1N/SPI1_MOSI/QUADSPI_BK1_IO2/LCD_SEG4 | PA7/OPAMP2_VINM/ADC12_IN12/TIM1_CH1N/TIM3_CH2/TIM8_CH1N/SPI1_MOSI/QUADSPI_BK1_IO2/LCD_SEG4/TIM17_CH1 | PA7/OPAMP2_VINM/ADC12_IN12/TIM1_CH1N/TIM3_CH2/TIM8_CH1N/SPI1_MOSI/QUADSPI_BK1_IO2/LCD_SEG4/TIM17_CH1
EVENTOUT | PA8 |  | MCO | TIM1_CH1 |  |  |  |  |  | USART1_CK |  |  | OTG_FS_SOF | LCD_COM0 |  |  | LPTIM2_OUT | PA8 | PA8 | PA8/MCO | PA8/MCO/TIM1_CH1 | PA8/MCO/TIM1_CH1 | PA8/MCO/TIM1_CH1 | PA8/MCO/TIM1_CH1 | PA8/MCO/TIM1_CH1 | PA8/MCO/TIM1_CH1 | PA8/MCO/TIM1_CH1/USART1_CK | PA8/MCO/TIM1_CH1/USART1_CK | PA8/MCO/TIM1_CH1/USART1_CK | PA8/MCO/TIM1_CH1/USART1_CK/OTG_FS_SOF | PA8/MCO/TIM1_CH1/USART1_CK/OTG_FS_SOF/LCD_COM0 | PA8/MCO/TIM1_CH1/USART1_CK/OTG_FS_SOF/LCD_COM0 | PA8/MCO/TIM1_CH1/USART1_CK/OTG_FS_SOF/LCD_COM0 | PA8/MCO/TIM1_CH1/USART1_CK/OTG_FS_SOF/LCD_COM0/LPTIM2_OUT | PA8/MCO/TIM1_CH1/USART1_CK/OTG_FS_SOF/LCD_COM0/LPTIM2_OUT
EVENTOUT | PA9 | OTG_FS_VBUS |  | TIM1_CH2 |  |  |  |  |  | USART1_TX |  |  |  | LCD_COM1 |  |  | TIM15_BKIN | PA9 | PA9/OTG_FS_VBUS | PA9/OTG_FS_VBUS | PA9/OTG_FS_VBUS/TIM1_CH2 | PA9/OTG_FS_VBUS/TIM1_CH2 | PA9/OTG_FS_VBUS/TIM1_CH2 | PA9/OTG_FS_VBUS/TIM1_CH2 | PA9/OTG_FS_VBUS/TIM1_CH2 | PA9/OTG_FS_VBUS/TIM1_CH2 | PA9/OTG_FS_VBUS/TIM1_CH2/USART1_TX | PA9/OTG_FS_VBUS/TIM1_CH2/USART1_TX | PA9/OTG_FS_VBUS/TIM1_CH2/USART1_TX | PA9/OTG_FS_VBUS/TIM1_CH2/USART1_TX | PA9/OTG_FS_VBUS/TIM1_CH2/USART1_TX/LCD_COM1 | PA9/OTG_FS_VBUS/TIM1_CH2/USART1_TX/LCD_COM1 | PA9/OTG_FS_VBUS/TIM1_CH2/USART1_TX/LCD_COM1 | PA9/OTG_FS_VBUS/TIM1_CH2/USART1_TX/LCD_COM1/TIM15_BKIN | PA9/OTG_FS_VBUS/TIM1_CH2/USART1_TX/LCD_COM1/TIM15_BKIN
EVENTOUT | PA10 |  |  | TIM1_CH3 |  |  |  |  |  | USART1_RX |  |  | OTG_FS_ID | LCD_COM2 |  |  | TIM17_BKIN | PA10 | PA10 | PA10 | PA10/TIM1_CH3 | PA10/TIM1_CH3 | PA10/TIM1_CH3 | PA10/TIM1_CH3 | PA10/TIM1_CH3 | PA10/TIM1_CH3 | PA10/TIM1_CH3/USART1_RX | PA10/TIM1_CH3/USART1_RX | PA10/TIM1_CH3/USART1_RX | PA10/TIM1_CH3/USART1_RX/OTG_FS_ID | PA10/TIM1_CH3/USART1_RX/OTG_FS_ID/LCD_COM2 | PA10/TIM1_CH3/USART1_RX/OTG_FS_ID/LCD_COM2 | PA10/TIM1_CH3/USART1_RX/OTG_FS_ID/LCD_COM2 | PA10/TIM1_CH3/USART1_RX/OTG_FS_ID/LCD_COM2/TIM17_BKIN | PA10/TIM1_CH3/USART1_RX/OTG_FS_ID/LCD_COM2/TIM17_BKIN
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

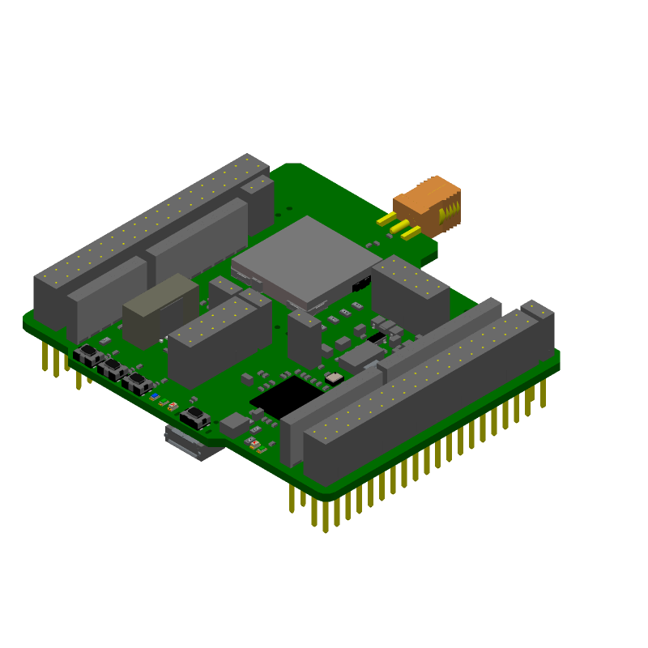
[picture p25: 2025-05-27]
Revision01/Hardware/Amplifier/Altium/AltiumLL/SamacSys_Images/3DM_13508188.png

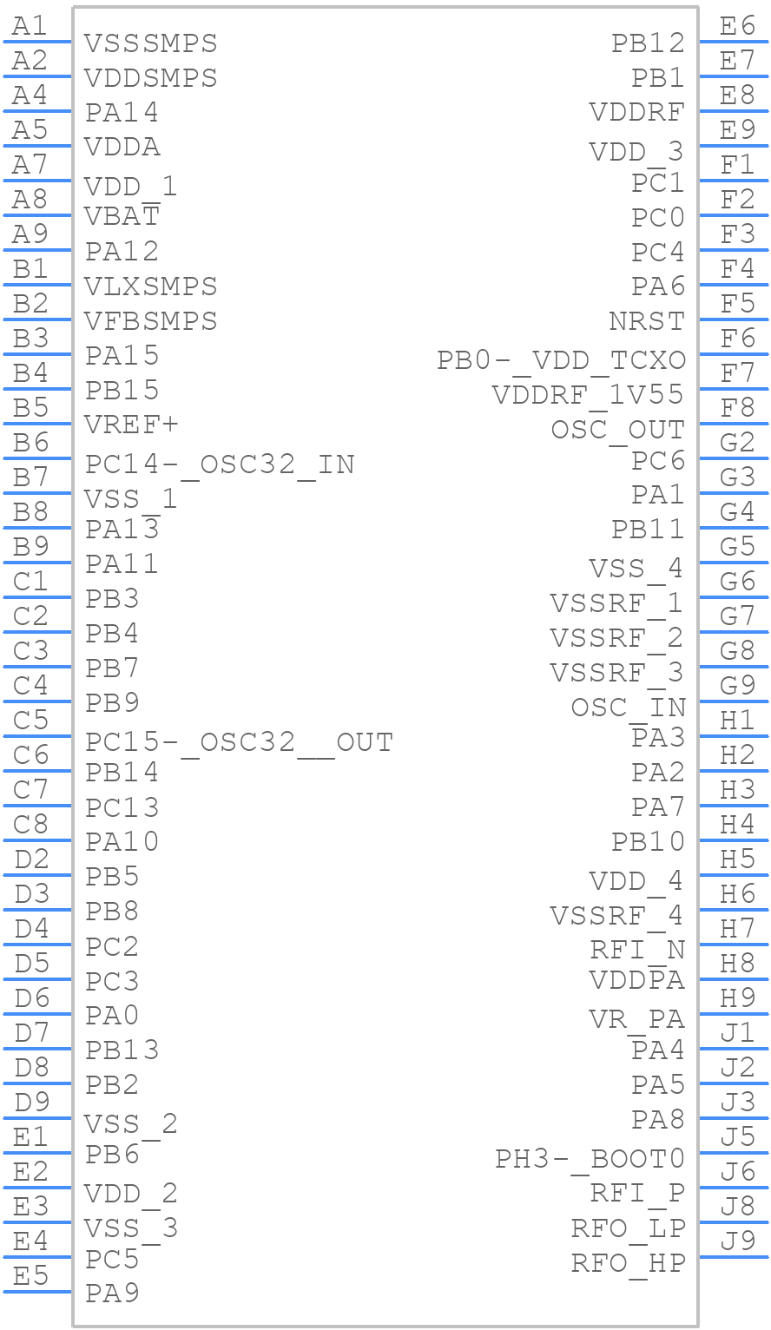
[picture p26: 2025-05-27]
Revision01/Hardware/Amplifier/Altium/AltiumLL/SamacSys_Images/SYM_18412912.png

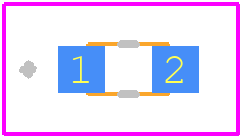
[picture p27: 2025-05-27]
Revision01/Hardware/Amplifier/Altium/AltiumLL/SamacSys_Images/PCB_294860.png

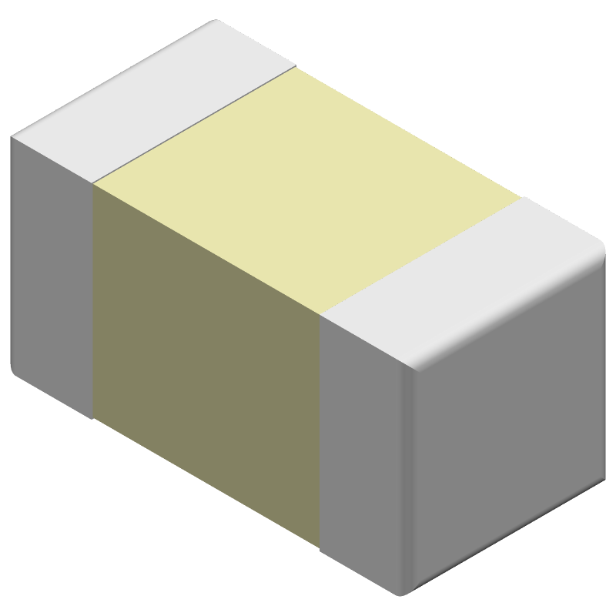
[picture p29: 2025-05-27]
Revision01/Hardware/Amplifier/Altium/AltiumLL/SamacSys_Images/3DM_2226447.png

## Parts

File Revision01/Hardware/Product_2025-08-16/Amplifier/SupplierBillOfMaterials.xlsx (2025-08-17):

# | Reference | Quantity | Qty | Qty Multiplier | Value | Description | Package | Footprint | Detailed Description | Datasheet | Manufacturer | Manufacturer Part Number | Mouser Link | Mouser Part Number | Exclude from BOM | DNP | Exclude from Board
1 | C1,C2 | 2 | 2 |  | 0.1uF | Multilayer Ceramic Capacitors MLCC - SMD/SMT 100nF+/-10% 50V X7R 0805 | 0805 (2012 Metric) | Capacitor_SMD:C_0805_2012Metric_Pad1.18x1.45mm_HandSolder |  | https://www.mouser.ca/datasheet/2/585/MLCC-1837944.pdf | Samsung Electro-Mechanics | CL21B104KBCNNWC | https://www.mouser.ca/ProductDetail/Samsung-Electro-Mechanics/CL21B104KBCNNWC?qs=yOVawPpwOwlu2UTVxWhmlw%3D%3D | 187-CL21B104KBCNNWC
2 | R1,R2,R4 | 3 | 3 |  | 1K +-0.1% | Thin Film Resistors - SMD .05W 1Kohms 0.1% 0805 25ppm | 0805 (2012 Metric) | Resistor_SMD:R_0805_2012Metric_Pad1.20x1.40mm_HandSolder |  | https://www.vishay.com/doc?28700 | Vishay / Beyschlag | MCU08050D1001BP500 | https://www.mouser.ca/ProductDetail/Vishay-Beyschlag/MCU08050D1001BP500?qs=70au2ePzUrEv3lkXFeCKsQ%3D%3D | 594-MCU0805D1001BP5
3 | R3 | 1 | 1 |  | 500 ± 5% | Thin Film Resistors - SMD .2W 499ohms .5% 0805 25ppm Auto | 0805 (2012 Metric) | Resistor_SMD:R_0805_2012Metric_Pad1.20x1.40mm_HandSolder |  | https://www.vishay.com/doc?28952 | Vishay / Beyschlag | MCU0805MD4990DP500 | https://www.mouser.ca/ProductDetail/Vishay-Beyschlag/MCU0805MD4990DP500?qs=EzBFWPtgsb1DD3PTBSGEVQ%3D%3D | 594-MCU0805MD4990DP5
4 | R5 | 1 | 1 |  | 20K +-0.1% | Thin Film Resistors - SMD 1/8W 20K Ohms 0.1% 0805 25ppm | 0805 (2012 Metric) | Resistor_SMD:R_0805_2012Metric_Pad1.20x1.40mm_HandSolder |  | https://www.mouser.ca/datasheet/2/392/n_catalog_partition01_en-1140338.pdf | Susumu | RG2012P-203-B-T5 | https://www.mouser.ca/ProductDetail/Susumu/RG2012P-203-B-T5?qs=juJhw1yPxAE0uzMTBmg8Hw%3D%3D | 754-RG2012P-203-B-T5
5 | R6 | 1 | 1 |  | 10K +-0.1% | Thin Film Resistors - SMD 1/8W 10K Ohms 0.1% 0805 25ppm | 0805 (2012 Metric) | Resistor_SMD:R_0805_2012Metric_Pad1.20x1.40mm_HandSolder |  | https://www.mouser.ca/datasheet/2/392/n_catalog_partition01_en-1140338.pdf | Susumu | RG2012P-103-B-T5 | https://www.mouser.ca/ProductDetail/Susumu/RG2012P-103-B-T5?qs=juJhw1yPxAHrnD3%252BNCg9%252Bw%3D%3D | 754-RG2012P-103-B-T5
6 | U2 | 1 | 1 |  | TLV9061SQDBVRQ1 | Operational Amplifiers - Op Amps Automotive single 5.5-V 10-MHz rail-to | SOT-23-6 | Package_TO_SOT_SMD:TSOT-23-6 |  | https://www.ti.com/lit/gpn/tlv9064-q1 | Texas Instruments | TLV9061SQDBVRQ1 | https://www.mouser.ca/ProductDetail/Texas-Instruments/TLV9061SQDBVRQ1?qs=DRkmTr78QASJ%252B5bCrdR4jA%3D%3D | 595-TLV9061SQDBVRQ1
7 | U1 | 1 | 1 |  | INA333AIDGKR | Instrumentation Amplifiers Lo Pwr Prec Inst Amp A 595-INA333AIDGKT | VSSOP-8 | Lib:INA333AIDGKR_SOP65P490X110-8N |  | https://www.ti.com/lit/gpn/ina333 | Texas Instruments | INA333AIDGKR | https://www.mouser.ca/ProductDetail/Texas-Instruments/INA333AIDGKR?qs=nJRxFdq%252BlvaKwfZOdHFpKg%3D%3D | 595-INA333AIDGKR
35 | U4 | 2 | 1 | 2 | Adafruit 3070 | RFM69HCW TRANSCEIVER RADIO BREAK | Module | Lib:Adafruit3070 | RFM69HCW - Transceiver 868MHz, 915MHz Evaluation Board | https://cdn-learn.adafruit.com/downloads/pdf/adafruit-rfm69hcw-and-rfm96-rfm95-rfm98-lora-packet-padio-breakouts.pdf | Adafruit Industries LLC | 3070 | https://www.mouser.ca/ProductDetail/Adafruit/3070?qs=AGnqjqvSJvLhs1q9K1razA%3D%3D | 485-3070 | https://www.digikey.ca/en/products/detail/adafruit-industries-llc/3070/6005355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 | 1528-1665-ND
 |  |  |  | NOTE: The Adafruit is unavailable on digikey at this time, so it is bundled with the 8x Amps

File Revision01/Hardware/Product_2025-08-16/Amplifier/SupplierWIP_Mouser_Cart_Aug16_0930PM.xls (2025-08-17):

SHOPPING CART
This is not an invoice
16-Aug-25 21:30:52
 | Mouser # | Mfr. # | Manufacturer | Customer # | Description | RoHS | Lifecycle | Order Qty. | Price (CAD) | Ext.: (CAD)
1 | 187-CL21B104KBCNNWC | CL21B104KBCNNWC | Samsung Electro-Mechanics |  | Multilayer Ceramic Capacitors MLCC - SMD/SMT 100nF+/-10% 50V X7R 0805 | RoHS Compliant |  | 16 | $0.036 | $0.58
2 | 594-MCU0805D1001BP5 | MCU08050D1001BP500 | Vishay |  | Thin Film Resistors - SMD .05W 1Kohms 0.1% 0805 25ppm | RoHS Compliant By Exemption |  | 24 | $0.274 | $6.58
3 | 594-MCU0805MD4990DP5 | MCU0805MD4990DP500 | Vishay |  | Thin Film Resistors - SMD .2W 499ohms .5% 0805 25ppm Auto | RoHS Compliant By Exemption |  | 8 | $0.174 | $1.39
4 | 754-RG2012P-203-B-T5 | RG2012P-203-B-T5 | Susumu |  | Thin Film Resistors - SMD 1/8W 20K Ohms 0.1% 0805 25ppm | RoHS Compliant |  | 8 | $0.145 | $1.16
5 | 754-RG2012P-103-B-T5 | RG2012P-103-B-T5 | Susumu |  | Thin Film Resistors - SMD 1/8W 10K Ohms 0.1% 0805 25ppm | RoHS Compliant |  | 8 | $0.145 | $1.16
6 | 595-TLV9061SQDBVRQ1 | TLV9061SQDBVRQ1 | Texas Instruments |  | Operational Amplifiers - Op Amps Automotive single 5.5-V 10-MHz rail-to | RoHS Compliant |  | 8 | $1.00 | $8.00
7 | 595-INA333AIDGKR | INA333AIDGKR | Texas Instruments |  | Instrumentation Amplifiers Lo Pwr Prec Inst Amp A 595-INA333AIDGKT | RoHS Compliant |  | 8 | $6.58 | $52.64
8 | 485-3070 | 3070 | Adafruit |  | Sub-GHz Development Tools Adafruit RFM69HCW Transceiver Radio Breakout - 868 or 915 MHz - RadioFruit | RoHS Compliant |  | 2 | $14.43 | $28.86
By submitting your order you agree to these terms and conditions. (https://www.mouser.ca/saleterms) |  |  |  |  |  |  |  |  | Merchandise: | $100.37
Prices are reflected at the date and time shown. |  |  |  |  |  |  |  |  | Shipping Charge: | $0.00

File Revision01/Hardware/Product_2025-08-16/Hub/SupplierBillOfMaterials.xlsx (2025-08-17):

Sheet: DigiKey
# | Reference | Quantity | Qty | Qty Multiplier | Value | Description | Package | Footprint | Detailed Description | Datasheet | Manufacturer | Manufacturer Part Number | Mouser Link | Mouser Part Number | DigiKey Link | DigiKey Part Number | AliExpress Link | AliExpress Part Number | DNP
1 | AE1 | 2 | 1 | 2 | ANT-916-CW-RCS-SMA | 915MHZ CCOMPACT RIGHT ANGLE WHIP | n/a |  | RF ANTENNA ISM, LoRaWAN, LPWA Whip, Right Angle SMA Male Connector Mount | https://www.te.com/commerce/DocumentDelivery/DDEController?Action=srchrtrv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 | TE Connectivity Linx | ANT-916-CW-RCS-SMA | https://www.mouser.ca/ProductDetail/TE-Connectivity-Linx-Technologies/ANT-916-CW-RCS-SMA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 | 712-ANT-916-CWRCSSMA | https://www.digikey.ca/en/products/detail/te-connectivity-linx/ANT-916-CW-RCS-SMA/16630288 | 343-ANT-916-CW-RCS-SMA-ND
3 | C1,C19 | 2 | 2 |  | 22uF ±10% | CAP CER 22UF 25V X5R 1206 | 1206 (3216 Metric) | Capacitor_SMD:C_1206_3216Metric_Pad1.33x1.80mm_HandSolder | 22 µF ±10% 25V Ceramic Capacitor X5R 1206 (3216 Metric) | https://mm.digikey.com/Volume0/opasdata/d220001/medias/docus/658/CL31A226KAHNNNE_Spec.pdf | Samsung Electro-Mechanics | CL31A226KAHNNNE | https://www.mouser.ca/ProductDetail/Samsung-Electro-Mechanics/CL31A226KAHNNNE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 | 187-CL31A226KAHNNNE | https://www.digikey.ca/en/products/detail/samsung-electro-mechanics/CL31A226KAHNNNE/3888705 | 1276-3047-1-ND
4 | C2,C4 | 2 | 2 |  | 1uF, X7R | CAP CER 1UF 50V X7R 0805 | 0805 (2012 Metric) | Capacitor_SMD:C_0805_2012Metric_Pad1.18x1.45mm_HandSolder | 1 µF ±10% 50V Ceramic Capacitor X7R 0805 (2012 Metric) | https://mm.digikey.com/Volume0/opasdata/d220001/medias/docus/609/CL21B105KBFNNNE_Spec.pdf | Samsung Electro-Mechanics | CL21B105KBFNNNE | https://www.mouser.ca/ProductDetail/Samsung-Electro-Mechanics/CL21B105KBFNNNE?qs=yOVawPpwOwmddQEBPU6Y9A%3D%3D | 187-CL21B105KBFNNNE | https://www.digikey.ca/en/products/detail/samsung-electro-mechanics/CL21B105KBFNNNE/3886687 | 1276-1029-1-ND
5 | C3,C6,C7,C10,C14 | 5 | 5 |  | 0.1uF ±10%, X7R | CAP CER 0.1UF 100V X7R 0805 | 0805 (2012 Metric) | Capacitor_SMD:C_0805_2012Metric_Pad1.18x1.45mm_HandSolder | 0.1 µF ±10% 100V Ceramic Capacitor X7R 0805 (2012 Metric) | https://mm.digikey.com/Volume0/opasdata/d220001/medias/docus/893/CL21B104KCFNNNE_Spec.pdf | Samsung Electro-Mechanics | CL21B104KCFNNNE | https://www.mouser.ca/ProductDetail/Samsung-Electro-Mechanics/CL21B104KCFNNNE?qs=lptGheUA4EwiEGVRX9oguw%3D%3D | 187-CL21B104KCFNNNE | https://www.digikey.ca/en/products/detail/samsung-electro-mechanics/CL21B104KCFNNNE/5961324 | 1276-6840-1-ND
6 | C5 | 1 | 1 |  | 10uF, X7R | CAP CER 10UF 25V X7R 1206 | 1206 (3216 Metric) | Capacitor_SMD:C_1206_3216Metric_Pad1.33x1.80mm_HandSolder | 10 µF ±10% 25V Ceramic Capacitor X7R 1206 (3216 Metric) | https://mm.digikey.com/Volume0/opasdata/d220001/medias/docus/658/CL31B106KAHNNNE_Spec.pdf | Samsung Electro-Mechanics | CL31B106KAHNNNE | https://www.mouser.ca/ProductDetail/Samsung-Electro-Mechanics/CL31B106KAHNNNE?qs=349EhDEZ59r5EZhnLOTsYA%3D%3D | 187-CL31B106KAHNNNE | https://www.digikey.ca/en/products/detail/samsung-electro-mechanics/CL31B106KAHNNNE/3887462 | 1276-1804-1-ND
7 | C8,C9,C11,C13,C15,C16,C17,C18 | 8 | 8 |  | 6.8nF ±10% | 6.8nF+/-10% 50V X7R 0603 | 0603 (1608 metric) | Capacitor_SMD:C_0603_1608Metric_Pad1.08x0.95mm_HandSolder | Multilayer Ceramic Capacitors MLCC - SMD/SMT 6.8nF+/-10% 50V X7R 0603 | https://www.mouser.ca/datasheet/2/585/MLCC-1837944.pdf | Samsung Electro-Mechanics | CL10B682KB8NNNC | https://mou.sr/3J8ffq3 | 187-CL10B682KB8NNNC | https://www.digikey.ca/en/products/detail/samsung-electro-mechanics/CL10B682KB8NNNC/3886843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 | 1276-1185-2-ND
8 | C12 | 1 | 1 |  | 10nF ±10%, Ceramic, X7R, >4V | CAP CER 10000PF 50V X7R 0603 | 0603 (1608 Metric) | Capacitor_SMD:C_0603_1608Metric_Pad1.08x0.95mm_HandSolder | 10000 pF ±10% 50V Ceramic Capacitor X7R 0603 (1608 Metric) | https://weblib.samsungsem.com/mlcc/mlcc-ec-data-sheet.do?partNumber=CL10B103KB8WPN | Samsung Electro-Mechanics | CL10B103KB8WPND | https://www.mouser.ca/ProductDetail/Samsung-Electro-Mechanics/CL10B103KB8WPND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 | 187-CL10B103KB8WPND | https://www.digikey.ca/en/products/detail/samsung-electro-mechanics/CL10B103KB8WPND/11487754 | 1276-CL10B103KB8WPNDCT-ND
9 | D1,D2,D3,D4,D5,D6,D7,D8,D9,D10,D11,D12,D13,D14,D15,D16 | 16 | 16 |  | D_Zener_Small | DIODE ZENER 3.3V 500MW SOD123 | SOD-123 | Diode_SMD:D_SOD-123 | Zener Diode 3.3 V 500 mW ±5% Surface Mount SOD-123 | https://www.diodes.com/datasheet/download/DDZ96xx-DDZ97xx.pdf | Diodes Incorporated | DDZ9684-7 | https://www.mouser.ca/ProductDetail/Diodes-Incorporated/DDZ9684-7?qs=mQbszxtPdlN5OVpmKRGZYw%3D%3D | 621-DDZ9684-7 | https://www.digikey.ca/en/products/detail/diodes-incorporated/DDZ9684-7/1934818 | DDZ9684-7DITR-ND
10 | F1 | 2 | 1 | 2 | FAST-BLOW 375mA 32V 0.45Ω | FUSE BOARD MNT 375MA 32VDC 0603 | 0603 (1608 Metric) | Fuse:Fuse_0603_1608Metric_Pad1.05x0.95mm_HandSolder | 375 mA 32 V Fuse Board Mount (Cartridge Style Excluded) Surface Mount 0603 (1608 Metric) | https://datasheets.kyocera-avx.com/AccuGuard2.pdf | KYOCERA AVX | F0603E0R37FSTR | https://www.mouser.ca/ProductDetail/KYOCERA-AVX/F0603E0R37FSTR?qs=vco6xy%252BeH1oeD3dI3xk78w%3D%3D | 581-F0603E0R37FSTR | https://www.digikey.ca/en/products/detail/kyocera-avx/F0603E0R37FSTR/768542 | 478-2859-1-ND
11 | F2 | 6 | 1 | 6 | 70mA 5s Fusing, 7.5 Ohms | FUSE BOARD MOUNT 28MA 63VDC 0603 | 0603 (1608 Metric) | Fuse:Fuse_0603_1608Metric_Pad1.05x0.95mm_HandSolder | 28 mA 63 V Fuse Board Mount (Cartridge Style Excluded) Surface Mount 0603 (1608 Metric) | https://datasheets.kyocera-avx.com/AccuGuardLC_0402.pdf | KYOCERA AVX | F0603G0R02FNTR | https://www.mouser.ca/ProductDetail/KYOCERA-AVX/F0603G0R02FNTR?qs=%252BdQmOuGyFcEJ7yNI5Fr0SQ%3D%3D | 581-F0603G0R02FNTR | https://www.digikey.ca/en/products/detail/kyocera-avx/F0603G0R02FNTR/9948432 | 478-13097-1-ND
12 | F3,F4,F5,F6,F7,F8,F9 | 7 | 7 |  | 70mA 5s Fusing, 7.5 Ohms | FUSE BOARD MOUNT 28MA 63VDC 0603 | 0603 (1608 Metric) | Fuse:Fuse_0603_1608Metric_Pad1.05x0.95mm_HandSolder | 28 mA 63 V Fuse Board Mount (Cartridge Style Excluded) Surface Mount 0603 (1608 Metric) | https://datasheets.kyocera-avx.com/AccuGuardLC_0402.pdf | KYOCERA AVX | F0603G0R02FNTR | https://www.mouser.ca/ProductDetail/KYOCERA-AVX/F0603G0R02FNTR?qs=%252BdQmOuGyFcEJ7yNI5Fr0SQ%3D%3D | 581-F0603G0R02FNTR | https://www.digikey.ca/en/products/detail/kyocera-avx/F0603G0R02FNTR/9948432 | 478-13097-1-ND
13 | J6,J7,J8,J9,J10,J11,J12,J13 | 8 | 8 |  | IDC 6Pin Male Header | CONN HEADER VERT 6POS 2.54MM | n/a | Lib:AdamTech_BHR-06-VUA | Connector Header Through Hole 6 position 0.100" (2.54mm)" | https://app.adam-tech.com/products/download/data_sheet/203218/bhr-xx-vua-data-sheet.pdf | Adam Tech | BHR-06-VUA | https://www.mouser.ca/ProductDetail/Adam-Tech/BHR-06-VUA?qs=HoCaDK9Nz5cobId%2FEjMHxg%3D%3D | 737-BHR-06-VUA | https://www.digikey.ca/en/products/detail/adam-tech/BHR-06-VUA/10414837 | 2057-BHR-06-VUA-ND
14 | J14,J16 | 16 | 2 | 8 | IDC 6Pin Male Header | CONN HEADER VERT 6POS 2.54MM | n/a | Lib:AdamTech_BHR-06-VUA | Connector Header Through Hole 6 position 0.100" (2.54mm)" | https://app.adam-tech.com/products/download/data_sheet/203218/bhr-xx-vua-data-sheet.pdf | Adam Tech | BHR-06-VUA | https://www.mouser.ca/ProductDetail/Adam-Tech/BHR-06-VUA?qs=HoCaDK9Nz5cobId%2FEjMHxg%3D%3D | 737-BHR-06-VUA | https://www.digikey.ca/en/products/detail/adam-tech/BHR-06-VUA/10414837 | 2057-BHR-06-VUA-ND
15 | J15,J17,J18 | 24 | 3 | 8 | IDC 6Pin Female Socket | SOCKET FLAT CABLE IDC 6P 2.54MM | n/a |  | 6 Position Rectangular Socket Connector IDC Gold | https://app.adam-tech.com/products/download/data_sheet/203410/fcs-xx-sg-data-sheet.pdf | Adam Tech | FCS-06-SG | https://www.mouser.ca/ProductDetail/Adam-Tech/FCS-06-SG?qs=xBpwZ0JX2zKrrDVVtBNx1A%3D%3D | 737-FCS-06-SG | https://www.digikey.ca/en/products/detail/adam-tech/FCS-06-SG/9832561 | 2057-FCS-06-SG-ND
16 | J19 | 2 | 1 | 2 | CON-SMA-EDGE-S | RF Connectors / Coaxial Connectors SMA Female PCB Edge Mount | n/a |  | SMA Connector Jack, Female Socket Board Edge, End Launch Solder | https://www.mouser.ca/datasheet/2/975/CON_SMA_EDGE_6_DATASHEET-3539198.pdf | RF Solutions | CON-SMA-EDGE-S | https://www.mouser.ca/ProductDetail/RF-Solutions/CON-SMA-EDGE-S?qs=UkDUCjYnTB3a941HfsgOOA%3D%3D | 223-CON-SMA-EDGE-S | https://www.digikey.ca/en/products/detail/rf-solutions/CON-SMA-EDGE-S/5845767 | CON-SMA-EDGE-S-ND
17 | L1 | 1 | 1 |  | 150uH | FIXED IND 150UH 330MA 2.64OHM SM | 1616 (4040 Metric) | Lib:LQH44PH151MPRL_IND_LQH44PN_PR_MUR-M | 150 µH Shielded Drum Core, Wirewound Inductor 330 mA 2.64Ohm Max 1616 (4040 Metric) | https://search.murata.co.jp/Ceramy/image/img/P02/JELF243A-9153.pdf | Murata Electronics | LQH44PH151MPRL | https://www.mouser.ca/ProductDetail/Murata-Electronics/LQH44PH151MPRL?qs=rkhjVJ6%2F3EJ9BU%2FIW%252BFNJA%3D%3D | 81-LQH44PH151MPRL | https://www.digikey.com/en/products/detail/murata-electronics/LQH44PH151MPRL/11690210 | 490-LQH44PH151MPRLCT-ND
18 | N1 | 1 | 1 |  | Battery Holder | BATT HOLDER 18650 4 CELL LEADS | n/a | Lib:BATT_HOLDER_18650_4_CELL_LEADS | Battery Holder (Open) 18650 4 Cell Wire Leads | https://mm.digikey.com/Volume0/opasdata/d220001/medias/docus/338/114090052_Web.pdf | Seeed Technology Co., Ltd | 114090052 | https://www.mouser.ca/ProductDetail/Seeed-Studio/114090052?qs=OTrKUuiFdkbetX%2F%2FZD%2Frtw%3D%3D | 713-114090052 | https://www.digikey.com/en/products/detail/seeed-technology-co-ltd/114090052/10451909 | 1597-114090052-ND
19 | Q1 | 1 | 1 |  | PMOS | MOSFET P-CH 20V 1.3A SOT23-3 | TO-236-3, SC-59, SOT-23-3 | Package_TO_SOT_SMD:TSOT-23 | P-Channel 20V 1.3A 400mW SOT-23-3 | https://www.onsemi.com/pdf/datasheet/ntr1p02lt1-d.pdf | onsemi | NVTR01P02LT1G | https://www.mouser.ca/ProductDetail/onsemi/NVTR01P02LT1G?qs=3PKVEWFFm2%2F%2FrLw71IHJjw%3D%3D | 863-NVTR01P02LT1G | https://www.digikey.ca/en/products/detail/onsemi/NVTR01P02LT1G/5969313?gclsrc=aw.ds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 | NVTR01P02LT1GOSCT-ND
20 | Q2 | 1 | 1 |  | NMOS | MOSFET N-CH 30V 500MA SOT23-3 | TO-236-3, SC-59, SOT-23-3 | Package_TO_SOT_SMD:TSOT-23 | N-Channel 30V 500mA 690mW SOT-23-3 | https://www.onsemi.com/pdf/datasheet/ntr4003n-d.pdf | onsemi | NTR4003NT1G | https://www.mouser.ca/ProductDetail/onsemi/NTR4003NT1G?qs=CBDP9nzV7kme%2Fyh64xROOQ%3D%3D | 863-NTR4003NT1G | https://www.digikey.ca/en/products/detail/onsemi/NTR4003NT3G/1967271?gclsrc=aw.ds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 | NTR4003NT3GOSCT-ND
21 | Q3 | 1 | 1 |  | PMOS | MOSFET P-CH 100V 600MA SOT23-3 | TO-236-3, SC-59, SOT-23-3 | Package_TO_SOT_SMD:TSOT-23 | P-Channel 100 V 600mA (Ta) 625mW (Ta) Surface Mount SOT-23-3 | https://www.diodes.com/assets/Datasheets/ZXMP10A13F.pdf | Diodes Incorporated | ZXMP10A13FTA | https://www.mouser.ca/ProductDetail/Diodes-Incorporated/ZXMP10A13FTA?qs=4zh0VFflF2ED5l%2FE78e7YQ%3D%3D | 522-ZXMP10A13FTA | https://www.digikey.ca/en/products/detail/diodes-incorporated/ZXMP10A13FTA/560644 | ZXMP10A13FTR-ND
22 | R1 | 1 | 1 |  | 0 | RES SMD 0 OHM JUMPER 1/2W 0805 | 0805 (2012 Metric) | Lib:ZeroOhmSwitch_R_0805_2012Metric_Pad1.20x1.40mm_HandSolder | 0 Ohms Jumper Chip Resistor 0805 (2012 Metric) Automotive AEC-Q200, Pulse Withstanding Thick Film | https://www.vishay.com/docs/20043/crcwhpe3.pdf | Vishay Dale | CRCW08050000Z0EA | https://www.mouser.ca/ProductDetail/Vishay/CRCW08050000Z0EA?qs=waxnFHLl2hB4NcTp6tAQPA%3D%3D | 71-CRCW0805-0-E3 | https://www.digikey.com/en/products/detail/vishay-dale/CRCW08050000Z0EAHP/2222316 | 541-0.0TBCT-ND
23 | R2,R11,R13,R15,R17,R19,R21,R23 | 8 | 8 |  | 100 ±1% | RES SMD 100 OHM 1% 1/8W 0805 | 0805 (2012 Metric) | Resistor_SMD:R_0805_2012Metric_Pad1.20x1.40mm_HandSolder | 100 Ohms ±1% 0.125W, 1/8W Chip Resistor 0805 (2012 Metric) Automotive AEC-Q200 Thick Film | https://www.vishay.com/docs/20035/dcrcwe3.pdf | Vishay Dale | CRCW0805100RFKEA | https://www.mouser.ca/ProductDetail/Vishay/CRCW0805100RFKEA?qs=LOX6nxTstiYDPDKmuLyNLw%3D%3D | 71-CRCW0805-100-E3 | https://www.digikey.ca/en/products/detail/vishay-dale/CRCW0805100RFKEA/1175523 | 541-100CCT-ND
24 | R3 | 1 | 1 |  | 76.8K+- 1%, ±100ppm/°C | RES SMD 76.8K OHM 1% 1/8W 0805 | 0805 (2012 Metric) | Resistor_SMD:R_0805_2012Metric_Pad1.20x1.40mm_HandSolder | 76.8 kOhms ±1% 0.125W, 1/8W Chip Resistor 0805 (2012 Metric) Automotive AEC-Q200 Thick Film | https://www.vishay.com/docs/20035/dcrcwe3.pdf | Vishay Dale | CRCW080576K8FKEA | https://www.mouser.ca/ProductDetail/Vishay/CRCW080576K8FKEA?qs=Lu3mkJd%252BoBETDVTzIaHY%2FQ%3D%3D | 71-CRCW080576K8FKEA | https://www.digikey.com/en/products/detail/vishay-dale/CRCW080576K8FKEA/1175852 | 541-76.8KCCT-ND
25 | R4 | 1 | 1 |  | 10K +-1%, ±100ppm/°C | RES 10K OHM 1% 1/8W 0805 | 0805 (2012 Metric) | Resistor_SMD:R_0805_2012Metric_Pad1.20x1.40mm_HandSolder | 10 kOhms ±1% 0.125W, 1/8W Chip Resistor 0805 (2012 Metric) Thick Film | https://www.vishay.com/docs/28773/crcwce3.pdf | Vishay Dale | CRCW080510K0FKEAC | https://www.mouser.ca/ProductDetail/Vishay/CRCW080510K0FKEAC?qs=E3Y5ESvWgWORadmUijPtxQ%3D%3D | 71-CRCW080510K0FKEAC | https://www.digikey.com/en/products/detail/vishay-dale/CRCW080510K0FKEAC/7928398 | 541-3976-1-ND
26 | R5,R7,R8 | 3 | 3 |  | 10K ±1% | RES SMD 10K OHM 1% 1/8W 0805 | 0805 (2012 Metric) | Resistor_SMD:R_0805_2012Metric_Pad1.20x1.40mm_HandSolder | 10 kOhms ±1% 0.125W, 1/8W Chip Resistor 0805 (2012 Metric) Automotive AEC-Q200 Thick Film | https://www.vishay.com/docs/20035/dcrcwe3.pdf | Vishay Dale | CRCW080510K0FKEA | https://www.mouser.ca/ProductDetail/Vishay/CRCW080510K0FKEA?qs=LOX6nxTstiZjDFtI%2F0c8Lw%3D%3D | 71-CRCW0805-10K-E3 | https://www.digikey.ca/en/products/detail/vishay-dale/CRCW080510K0FKEA/1175751 | 541-10.0KCCT-ND
27 | R6 | 1 | 1 |  | 15K ±1% | RES SMD 15K OHM 1% 1/8W 0805 | 0805 (2012 Metric) | Resistor_SMD:R_0805_2012Metric_Pad1.20x1.40mm_HandSolder | 15 kOhms ±1% 0.125W, 1/8W Chip Resistor 0805 (2012 Metric) Automotive AEC-Q200 Thick Film | https://www.vishay.com/docs/20035/dcrcwe3.pdf | Vishay Dale | CRCW080515K0FKEA | https://www.mouser.ca/ProductDetail/Vishay/CRCW080515K0FKEA?qs=bMjB6bAaLEM4rXT2DoR3BA%3D%3D | 71-CRCW0805-15K-E3 | https://www.digikey.ca/en/products/detail/vishay-dale/CRCW080515K0FKEA/1175769 | 541-15.0KCCT-ND
28 | R9 | 1 | 1 |  | 5K ±1% | RES SMD 5K OHM 1% 1/8W 0805 | 0805 (2012 Metric) | Resistor_SMD:R_0805_2012Metric_Pad1.20x1.40mm_HandSolder | 5 kOhms ±1% 0.125W, 1/8W Chip Resistor 0805 (2012 Metric) Automotive AEC-Q200 Thick Film | https://www.vishay.com/docs/20008/dcrcw.pdf | Vishay Dale | CRCW08055K00FKTA | https://www.mouser.ca/ProductDetail/Vishay/CRCW08055K00FKTA?qs=O7pb%252BE5gJ7THvgJkhh%2F2MQ%3D%3D | 71-CRCW0805-5K | https://www.digikey.ca/en/products/detail/vishay-dale/CRCW08055K00FKTA/5075661 | 541-CRCW08055K00FKTACT-ND
30 | R12,R14,R16,R18,R20,R22,R24,R26 | 8 | 8 |  | 1M ±1% | RES SMD 1M OHM 1% 1/8W 0805 | 0805 (2012 Metric) | Resistor_SMD:R_0805_2012Metric_Pad1.20x1.40mm_HandSolder | 1 MOhms ±1% 0.125W, 1/8W Chip Resistor 0805 (2012 Metric) Automotive AEC-Q200 Thick Film | https://www.vishay.com/docs/20035/dcrcwe3.pdf | Vishay Dale | CRCW08051M00FKEA | https://www.mouser.ca/ProductDetail/Vishay/CRCW08051M00FKEA?qs=1CkV0QOCgMoYllQJ5f1DKQ%3D%3D | 71-CRCW0805-1.0M-E3 | https://www.digikey.ca/en/products/detail/vishay-dale/CRCW08051M00FKEA/1176016 | 541-1.00MCCT-ND
31 | SW1 | 1 | 1 |  | ON/OFF_SW_SPST_LED | SWITCH ROCKER SPST-NO 20A 12V | n/a | Connector_PinHeader_2.54mm:PinHeader_1x04_P2.54mm_Vertical | Rocker Switch SPST-NO 20A (DC) Panel Mount, Snap-In | https://mm.digikey.com/Volume0/opasdata/d220001/medias/docus/6662/432_V%20Datasheet.pdf | Carling Technologies | V2D2S00B-GZCAD-100-XACT1 | No Results | No Results | https://www.digikey.ca/en/products/detail/carling-technologies/V2D2S00B-GZCAD-100-XACT1/11481760 | 432-V2D2S00B-GZCAD-100-XACT1-ND |  |  | DNP
32 | U1 | 2 | 1 | 2 | NUCLEO-L476RG | NUCLEO-64 STM32L476RG EVAL BRD | n/a | Lib:MODULE_NUCLEO-L476RG | STM32L476 Nucleo-64 STM32L4 ARM® Cortex®-M4 MCU 32-Bit Embedded Evaluation Board | https://www.st.com/content/ccc/resource/technical/document/data_brief/c8/3c/30/f7/d6/08/4a/26/DM00105918.pdf/files/DM00105918.pdf/jcr:content/translations/en.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 | STMicroelectronics | NUCLEO-L476RG | https://www.mouser.ca/ProductDetail/STMicroelectronics/NUCLEO-L476RG?qs=PRtH0mD6DWbM6mRV5DKjBQ%3D%3D | 511-NUCLEO-L476RG | https://www.digikey.ca/en/products/detail/stmicroelectronics/NUCLEO-L476RG/5347711 | 497-15881-ND
33 | U2 | 1 | 1 |  | LMR51603XFDBVR | IC REG BUCK ADJ 600MA SOT23-6 | SOT-23-6 | Lib:LMR51603XFDBVR_DBV0006A-MFG-IPC_C | Buck Switching Regulator IC Positive Adjustable 0.8V 1 Output 600mA SOT-23-6 | https://www.ti.com/lit/ds/symlink/lmr51606.pdf?ts=1704242784728 | Texas Instruments | LMR51606XDBVR | https://www.mouser.ca/ProductDetail/Texas-Instruments/LMR51606XDBVR?qs=mELouGlnn3eccxHdZD5yuw%3D%3D | 595-LMR51606XDBVR | https://www.digikey.ca/en/products/detail/texas-instruments/LMR51606XDBVR | 296-LMR51606XDBVRCT-ND
34 | U3 | 1 | 1 |  | MPU-6500 | IMU ACCEL/GYRO 3-AXIS I2C 24QFN | 24-VFQFN Module Exposed Pad | Lib:MPU-6500_QFN40P300X300X95-25N | Accelerometer, Gyroscope, 6 Axis Sensor I2C, SPI Output | https://invensense.tdk.com/wp-content/uploads/2020/06/PS-MPU-6500A-01-v1.3.pdf | TDK InvenSense | MPU-6500 | https://www.mouser.ca/ProductDetail/TDK-InvenSense/MPU-6500?qs=u4fy%2FsgLU9PiIOIlWOSPhQ%3D%3D | 410-MPU-6500 | https://www.digikey.ca/en/products/detail/tdk-invensense/MPU-6500/4385413?gad_source=1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 | 1428-1011-1-ND
 |  |  |  |  | NOTE: The Adafruit is unavailable on digikey at this time, so it is bundled with the 8x Amps
 |  |  |  |  | NOTE: Also added the BH26AAB as present in the other .csv BOM. I was too lazy to redo this sheet again, it's just a battery holder for 6x AA batteries for 3$

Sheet: Mouser
# | Reference | Quantity | Qty | Qty Multiplier | Value | Description | Package | Footprint | Detailed Description | Datasheet | Manufacturer | Manufacturer Part Number | Mouser Link | Mouser Part Number | DigiKey Link | DigiKey Part Number | AliExpress Link | AliExpress Part Number | DNP
32 | U1 | 2 | 1 | 2 | NUCLEO-L476RG | NUCLEO-64 STM32L476RG EVAL BRD | n/a | Lib:MODULE_NUCLEO-L476RG | STM32L476 Nucleo-64 STM32L4 ARM® Cortex®-M4 MCU 32-Bit Embedded Evaluation Board | https://www.st.com/content/ccc/resource/technical/document/data_brief/c8/3c/30/f7/d6/08/4a/26/DM00105918.pdf/files/DM00105918.pdf/jcr:content/translations/en.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 | STMicroelectronics | NUCLEO-L476RG | https://www.mouser.ca/ProductDetail/STMicroelectronics/NUCLEO-L476RG?qs=PRtH0mD6DWbM6mRV5DKjBQ%3D%3D | 511-NUCLEO-L476RG | https://www.digikey.ca/en/products/detail/stmicroelectronics/NUCLEO-L476RG/5347711 | 497-15881-ND
35 | U4 | 2 | 1 | 2 | Adafruit 3070 | RFM69HCW TRANSCEIVER RADIO BREAK | Module | Lib:Adafruit3070 | RFM69HCW - Transceiver 868MHz, 915MHz Evaluation Board | https://cdn-learn.adafruit.com/downloads/pdf/adafruit-rfm69hcw-and-rfm96-rfm95-rfm98-lora-packet-padio-breakouts.pdf | Adafruit Industries LLC | 3070 | https://www.mouser.ca/ProductDetail/Adafruit/3070?qs=AGnqjqvSJvLhs1q9K1razA%3D%3D | 485-3070 | https://www.digikey.ca/en/products/detail/adafruit-industries-llc/3070/6005355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 | 1528-1665-ND
 | NOTE: The Adafruit is unavailable on digikey at this time, so it is bundled with the 8x Amps
 | NOTE: The two NUCLEOs are to make sure the order is over the 100$ CAD shipping savings.

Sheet: AliExpress
# | Reference | Quantity | Qty | Qty Multiplier | Value | Description | Package | Footprint | Detailed Description | Datasheet | Manufacturer | Manufacturer Part Number | Mouser Link | Mouser Part Number | DigiKey Link | DigiKey Part Number | AliExpress Link | AliExpress Part Number | DNP
2 | BT1 | 1 | 1 |  | 18650 Sodium-ion 3V 1500mAh | 18650 Sodium-ion 3V 1500mAh | 18650 | Connector_PinHeader_2.54mm:PinHeader_1x02_P2.54mm_Vertical | 18650 Sodium Battery 3V 1500mAh SIB Rechargeable Cell 3000+Cycles NA-ion Batteries for Energy Storage E-Bike Scooter Toy Cars | https://www.aliexpress.com/item/1005005859082063.html | SelianEnergy Lifepo4 Battery Store | 18650 Sodium-ion 3V 1500mAh |  |  | https://www.aliexpress.com/item/1005005859082063.html |  | https://www.aliexpress.com/item/1005005859082063.html | Color: 3V 1500mAh 4PCS
29 | R10 | 16 | 1 | 16 | Full Bridge Strain Gauge 350 ohm | Full Bridge Strain Gauge 350 ohm | n/a |  | 1PCS BHF/BF350-3EB-AWG Full Bridge Strain Gauge Foil 350 ohm Strain Gauge High Precision Pressure Sensor | https://www.aliexpress.com/item/1005006546478858.html | Brand Name ZDA | BF350-3EB-AWG |  |  | https://www.aliexpress.com/item/1005006546478858.html |  | https://www.aliexpress.com/item/1005006546478858.html | BF350-3EB-AWG 1PCS

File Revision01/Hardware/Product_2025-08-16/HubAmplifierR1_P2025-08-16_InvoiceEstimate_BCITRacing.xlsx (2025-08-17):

INVOICE |  | From: | Cinevance Technologies Inc.
**ESTIMATE** |  |  | 5750 Hastings Street
 |  |  | Burnaby, BC
 |  |  | Dan Mahmoud
 |  |  | (778) 583 6988
 |  |  | dan@cinevance.ca
Invoice For: | BCIT Racing | Invoice ID | HubAmplifierR1_P2025-08-16
 | Burnaby, BC | Issue Date | 2025-08-17 11:59
 |  | Currency | CAD
 |  | Terms | Due upon receipt
DESCRIPTION |  | QUANTITY | UNIT PRICE | AMOUNT
Components: Mouser: 8xAmplifier + 2xAdafruit 3070 |  | 1.00 | $100.37 | $100.37
Components: Digi-Key: 2xHub |  | 1.00 | $145.69 | $145.69
Circuit Board: PCBWay: 10xAmplifier + 5xHub |  | 1.00 | $107.35 | $107.35
Components: AliExpress: 16xStrainGauges + 4xSodiumBattery |  | 1.00 | $56.14 | $56.14
 |  |  |  | $0.00
 |  |  |  | $0.00
 |  |  |  | $0.00
 |  |  |  | $0.00
 |  |  |  | $0.00
SUBTOTAL |  |  |  | $409.55
TAX RATE
 |  |  | TAX | $0.00
AMOUNT DUE |  |  |  | $409.55
Notes:

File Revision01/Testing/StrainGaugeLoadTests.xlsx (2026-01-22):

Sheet: Analysis
Applied Force (lbs) | Strain gauge Differential Voltage (mV)
0.00 | 0.00000000
1000.00 | 4.18000000
2000.00 | 7.74000000
3000.00 | 11.36000000
4000.00 | 15.08000000
5000.00 | 18.72000000
6000.00 | 22.36000000
7000.00 | 26.12000000
8000.00 | 30.01000000
7000.00 | 27.13000000
6000.00 | 23.12000000
5000.00 | 20.06000000
4000.00 | 16.57000000
3000.00 | 12.94000000
2000.00 | 9.49000000
1000.00 | 5.22000000
0.00 | 0.70000000
Applied Force (lbs) | Differential amplified Voltage (V)
0.00 | 1.42000000
1000.00 | 1.52000000
2000.00 | 1.68000000
3000.00 | 1.84000000
4000.00 | 2.00000000
5000.00 | 2.16000000
6000.00 | 2.32000000
7000.00 | 2.49000000
8000.00 | 2.63000000
8000.00 | 2.64000000
7000.00 | 2.56000000
6000.00 | 2.35000000
5000.00 | 2.22000000
4000.00 | 2.04000000
3000.00 | 1.90000000
2000.00 | 1.74000000
1000.00 | 1.56000000
0.00 | 1.42000000

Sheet: Double Analysis
Name: |  |  |  |  |  |  | 2026-01-21
First Dataset |  | Second Dataset
X Values | Y Values | X Values | Y Values |  |  |  |  | Fit Equation:
 |  |  |  |  |  |  |  | y=A+Bx+Cx²
 |  |  |  |  |  | First Dataset Fit
 |  |  |  |  |  |  | Value | Uncertainty | CD: | 0.00%
 |  |  |  |  |  | A | 0 | 0
 |  |  |  |  |  | B | 0 | 0
 |  |  |  |  |  | C |  | 0
 |  |  |  | Power for fixed power fit:
 |  |  |  |  | 1 | Second Dataset Fit
 |  |  |  |  |  |  | Value | Uncertainty | CD: | 0.00%
 |  |  |  |  |  | A | 0 | 0
 |  |  |  |  |  | B | 0 | 0
 |  |  |  |  |  | C |  | 0

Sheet: Comparison
Name: |  |  |  | 2026-01-21
№ | Source | Value (unit) | Uncertainty
1
2
3
4
5
6

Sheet: Manual Fitting
Name: |  |  |  |  | 2026-01-21
X Values | Y Values
 |  | Fit Type | Fit Function
 |  |  | y=A+Bx
 |  |  | Parameter | Manual Estimate |  | CD:
 |  |  | A | 0.00
 |  |  | B | 0.04

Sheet: Guts
Fit type |  |  | 8 |  |  | x-values | fit y-values | DA x-values | fit 1 y-values | fit 2 y-values | x-data | y-data | freeform y | w/ duplicates | de-duplicated | DAx1data | DAy1data | DAx2data | DAy2data | DAx1 | DAx1 order | DAy1 match | Frform DAy1 | DAx2 | DAx2 order | DAy2 match | Frform DAy2 | Fit type | 1 | m.f. x-plot | m.f. fit y | m.f. xData | m.f. yData | m.f. y fit | m.f. sq res | (y_i-y_av)^2
Last row with x data |  |  | 40 |  | 0 | 0.00 | #N/A | #N/A | #N/A | #N/A | 0 | 0.70000000 | #N/A | 0.00 | 1e-13 | #N/A | #N/A | #N/A | #N/A |  | #N/A | #N/A | #N/A |  | #N/A | #N/A | #N/A | Optimize? | 1 | 0.00 | 0.00 | #N/A | #N/A | #N/A | #N/A | #N/A
Last row with y data |  |  | 40 |  | 1 | 80.00 | #N/A | #N/A | #N/A | #N/A | 1e-13 | 0.00000000 | #N/A | 1000.00 | 1000.00 |  |  |  |  |  | #N/A | #N/A | #N/A |  | #N/A | #N/A | #N/A |  |  | 0.00 | 0.00 |  |  | 0.00 | 0 | #N/A
Last row with paired data |  |  | 40 |  | 2 | 160.00 | #N/A | #N/A | #N/A | #N/A | 1000 | 5.22000000 | #N/A | 2000.00 | 2000.00 |  |  |  |  |  | #N/A | #N/A | #N/A |  | #N/A | #N/A | #N/A |  |  | 0.00 | 0.00 |  |  | 0.00 | 0 | #N/A
First row with x data |  |  | 2 |  | 3 | 240.00 | #N/A | #N/A | #N/A | #N/A | 1000 | 4.18000000 | #N/A | 3000.00 | 3000.00 |  |  |  |  |  | #N/A | #N/A | #N/A |  | #N/A | #N/A | #N/A | linear | y=A+Bx | 0.00 | 0.00 |  |  | 0.00 | 0 | #N/A
First row with y data |  |  | 2 |  | 4 | 320.00 | #N/A | #N/A | #N/A | #N/A | 2000 | 7.74000000 | #N/A | 4000.00 | 4000.00 |  |  |  |  |  | #N/A | #N/A | #N/A |  | #N/A | #N/A | #N/A | lorentzian | y=A/(1+((x−B)/C)²) | 0.00 | 0.00 |  |  | 0.00 | 0 | #N/A
First row with paired data |  |  | 2 |  | 5 | 400.00 | #N/A | #N/A | #N/A | #N/A | 2000 | 7.74000000 | #N/A | 5000.00 | 5000.00 |  |  |  |  |  | #N/A | #N/A | #N/A |  | #N/A | #N/A | #N/A | gaussian | y=A exp(−((x−B)/C)²) | 0.00 | 0.00 |  |  | 0.00 | 0 | #N/A
 |  |  |  |  | 6 | 480.00 | #N/A | #N/A | #N/A | #N/A | 3000 | 11.36000000 | #N/A | 6000.00 | 6000.00 |  |  |  |  |  | #N/A | #N/A | #N/A |  | #N/A | #N/A | #N/A | sine | y=A sin(Bx−C)+D | 0.00 | 0.00 |  |  | 0.00 | 0 | #N/A
 |  |  |  |  | 7 | 560.00 | #N/A | #N/A | #N/A | #N/A | 3000 | 11.36000000 | #N/A | 7000.00 | 7000.00 |  |  |  |  |  | #N/A | #N/A | #N/A |  | #N/A | #N/A | #N/A |  |  | 0.00 | 0.00 |  |  | 0.00 | 0 | #N/A
Analysis fit parameters |  |  |  |  | 8 | 640.00 | #N/A | #N/A | #N/A | #N/A | 4000 | 15.08000000 | #N/A | 8000.00 | 8000.00 |  |  |  |  |  | #N/A | #N/A | #N/A |  | #N/A | #N/A | #N/A |  |  | 0.00 | 0.00 |  |  | 0.00 | 0 | #N/A
coeffs | #N/A |  |  |  | 9 | 720.00 | #N/A | #N/A | #N/A | #N/A | 4000 | 15.08000000 | #N/A | 7000.00 | 7000.00 |  |  |  |  |  | #N/A | #N/A | #N/A |  | #N/A | #N/A | #N/A | #N/A |  | 0.00 | 0.00 |  |  | 0.00 | 0 | #N/A
unc. |  |  |  |  | 10 | 800.00 | #N/A | #N/A | #N/A | #N/A | 5000 | 18.72000000 | #N/A | 6000.00 | 6000.00 |  |  |  |  |  | #N/A | #N/A | #N/A |  | #N/A | #N/A | #N/A |  |  | 0.00 | 0.00 |  |  | 0.00 | 0 | #N/A
stats |  |  |  |  | 11 | 880.00 | #N/A | #N/A | #N/A | #N/A | 5000 | 18.72000000 | #N/A | 5000.00 | 5000.00 |  |  |  |  |  | #N/A | #N/A | #N/A |  | #N/A | #N/A | #N/A |  |  | 0.00 | 0.00 |  |  | 0.00 | 0 | #N/A
 |  |  |  |  | 12 | 960.00 | #N/A | #N/A | #N/A | #N/A | 6000 | 22.36000000 | #N/A | 4000.00 | 4000.00 |  |  |  |  |  | #N/A | #N/A | #N/A |  | #N/A | #N/A | #N/A | guessed | solved | 0.00 | 0.00 |  |  | 0.00 | 0 | #N/A
 |  |  |  |  | 13 | 1040.00 | #N/A | #N/A | #N/A | #N/A | 6000 | 22.36000000 | #N/A | 3000.00 | 3000.00 |  |  |  |  |  | #N/A | #N/A | #N/A |  | #N/A | #N/A | #N/A | 0.00 | 6264.798219 | 0.00 | 0.00 |  |  | 0.00 | 0 | #N/A
 |  |  |  |  | 14 | 1120.00 | #N/A | #N/A | #N/A | #N/A | 7000 | 26.12000000 | #N/A | 2000.00 | 2000.00 |  |  |  |  |  | #N/A | #N/A | #N/A |  | #N/A | #N/A | #N/A | 0.04 | 10.46591908 | 0.00 | 0.00 |  |  | 0.00 | 0 | #N/A
 |  |  |  |  | 15 | 1200.00 | #N/A | #N/A | #N/A | #N/A | 7000 | 26.12000000 | #N/A | 1000.00 | 1000.00 |  |  |  |  |  | #N/A | #N/A | #N/A |  | #N/A | #N/A | #N/A | #N/A | 0.3820246435 | 0.00 | 0.00 |  |  | 0.00 | 0 | #N/A
 |  |  |  |  | 16 | 1280.00 | #N/A | #N/A | #N/A | #N/A | 8000 | 30.01000000 | #N/A | 0.00 | 0.00 |  |  |  |  |  | #N/A | #N/A | #N/A |  | #N/A | #N/A | #N/A | #N/A | #N/A | 0.00 | 0.00 |  |  | 0.00 | 0 | #N/A
 |  |  |  |  | 17 | 1360.00 | #N/A | #N/A | #N/A | #N/A | #N/A | #N/A | #N/A |  |  |  |  |  |  |  | #N/A | #N/A | #N/A |  | #N/A | #N/A | #N/A |  |  | 0.00 | 0.00 |  |  | 0.00 | 0 | #N/A
 |  |  |  |  | 18 | 1440.00 | #N/A | #N/A | #N/A | #N/A | #N/A | #N/A | #N/A |  |  |  |  |  |  |  | #N/A | #N/A | #N/A |  | #N/A | #N/A | #N/A |  |  | 0.00 | 0.00 |  |  | 0.00 | 0 | #N/A
 |  | Fits available |  |  | 19 | 1520.00 | #N/A | #N/A | #N/A | #N/A | #N/A | #N/A | #N/A |  |  |  |  |  |  |  | #N/A | #N/A | #N/A |  | #N/A | #N/A | #N/A |  |  | 0.00 | 0.00 |  |  | 0.00 | 0 | #N/A
 | 1 | y=A+Bx |  |  | 20 | 1600.00 | #N/A | #N/A | #N/A | #N/A | #N/A | #N/A | #N/A |  |  |  |  |  |  |  | #N/A | #N/A | #N/A |  | #N/A | #N/A | #N/A |  | #N/A | 0.00 | 0.00 |  |  | 0.00 | 0 | #N/A
 | 2 | #REF! |  | y=A | 21 | 1680.00 | #N/A | #N/A | #N/A | #N/A | #N/A | #N/A | #N/A |  |  |  |  |  |  |  | #N/A | #N/A | #N/A |  | #N/A | #N/A | #N/A |  |  | 0.00 | 0.00 |  |  | 0.00 | 0 | #N/A
 | 3 | y=A+Bx+Cx² |  | y=Bx | 22 | 1760.00 | #N/A | #N/A | #N/A | #N/A | #N/A | #N/A | #N/A |  |  |  |  |  |  |  | #N/A | #N/A | #N/A |  | #N/A | #N/A | #N/A |  |  | 0.00 | 0.00 |  |  | 0.00 | 0 | #N/A
 | 4 | y=A+Bx+Cx²+Dx³ |  | y=Cx² | 23 | 1840.00 | #N/A | #N/A | #N/A | #N/A | #N/A | #N/A | #N/A |  |  |  |  |  |  |  | #N/A | #N/A | #N/A |  | #N/A | #N/A | #N/A |  |  | 0.00 | 0.00 |  |  | 0.00 | 0 | #N/A
 | 5 | y=Axᴮ |  | y=Dx³ | 24 | 1920.00 | #N/A | #N/A | #N/A | #N/A | #N/A | #N/A | #N/A |  |  |  |  |  |  |  | #N/A | #N/A | #N/A |  | #N/A | #N/A | #N/A |  |  | 0.00 | 0.00 |  |  | 0.00 | 0 | #N/A
 | 6 | y=Aeᴮˣ |  | y=Ex⁴ | 25 | 2000.00 | #N/A | #N/A | #N/A | #N/A | #N/A | #N/A | #N/A |  |  |  |  |  |  |  | #N/A | #N/A | #N/A |  | #N/A | #N/A | #N/A |  |  | 0.00 | 0.00 |  |  | 0.00 | 0 | #N/A
 | 7 | No fitting |  |  | 26 | 2080.00 | #N/A | #N/A | #N/A | #N/A | #N/A | #N/A | #N/A |  |  |  |  |  |  |  | #N/A | #N/A | #N/A |  | #N/A | #N/A | #N/A |  |  | 0.00 | 0.00 |  |  | 0.00 | 0 | #N/A
 | 8 | No fitting |  |  | 27 | 2160.00 | #N/A | #N/A | #N/A | #N/A | #N/A | #N/A | #N/A |  |  |  |  |  |  |  | #N/A | #N/A | #N/A |  | #N/A | #N/A | #N/A |  |  | 0.00 | 0.00 |  |  | 0.00 | 0 | #N/A
 |  |  |  |  | 28 | 2240.00 | #N/A | #N/A | #N/A | #N/A | #N/A | #N/A | #N/A |  |  |  |  |  |  |  | #N/A | #N/A | #N/A |  | #N/A | #N/A | #N/A |  |  | 0.00 | 0.00 |  |  | 0.00 | 0 | #N/A
 | Double Fit Info |  |  |  | 29 | 2320.00 | #N/A | #N/A | #N/A | #N/A | #N/A | #N/A | #N/A |  |  |  |  |  |  |  | #N/A | #N/A | #N/A |  | #N/A | #N/A | #N/A |  |  | 0.00 | 0.00 |  |  | 0.00 | 0 | #N/A
Fit type |  |  | 2 |  | 30 | 2400.00 | #N/A | #N/A | #N/A | #N/A | #N/A | #N/A | #N/A |  |  |  |  |  |  |  | #N/A | #N/A | #N/A |  | #N/A | #N/A | #N/A |  |  | 0.00 | 0.00 |  |  | 0.00 | 0 | #N/A
Last row with x1 data |  |  | #N/A |  | 31 | 2480.00 | #N/A | #N/A | #N/A | #N/A | #N/A | #N/A | #N/A |  |  |  |  |  |  |  | #N/A | #N/A | #N/A |  | #N/A | #N/A | #N/A |  |  | 0.00 | 0.00 |  |  | 0.00 | 0 | #N/A
Last row with y1 data |  |  | #N/A |  | 32 | 2560.00 | #N/A | #N/A | #N/A | #N/A | #N/A | #N/A | #N/A |  |  |  |  |  |  |  | #N/A | #N/A | #N/A |  | #N/A | #N/A | #N/A |  |  | 0.00 | 0.00 |  |  | 0.00 | 0 | #N/A
Last row with paired 1st set data |  |  | #N/A |  | 33 | 2640.00 | #N/A | #N/A | #N/A | #N/A | #N/A | #N/A | #N/A |  |  |  |  |  |  |  | #N/A | #N/A | #N/A |  | #N/A | #N/A | #N/A |  |  | 0.00 | 0.00 |  |  | 0.00 | 0 | #N/A
First row with x1 data |  |  | #N/A |  | 34 | 2720.00 | #N/A | #N/A | #N/A | #N/A | #N/A | #N/A | #N/A |  |  |  |  |  |  |  | #N/A | #N/A | #N/A |  | #N/A | #N/A | #N/A |  |  | 0.00 | 0.00 |  |  | 0.00 | 0 | #N/A
First row with y1 data |  |  | #N/A |  | 35 | 2800.00 | #N/A | #N/A | #N/A | #N/A | #N/A | #N/A | #N/A |  |  |  |  |  |  |  | #N/A | #N/A | #N/A |  | #N/A | #N/A | #N/A |  |  | 0.00 | 0.00 |  |  | 0.00 | 0 | #N/A
First row with paired 1st set data |  |  | #N/A |  | 36 | 2880.00 | #N/A | #N/A | #N/A | #N/A | #N/A | #N/A | #N/A |  |  |  |  |  |  |  | #N/A | #N/A | #N/A |  | #N/A | #N/A | #N/A |  |  | 0.00 | 0.00 |  |  | 0.00 | 0 | #N/A
Last row with x2 data |  |  | #N/A |  | 37 | 2960.00 | #N/A | #N/A | #N/A | #N/A | #N/A | #N/A | #N/A |  |  |  |  |  |  |  | #N/A | #N/A | #N/A |  | #N/A | #N/A | #N/A |  |  | 0.00 | 0.00 |  |  | 0.00 | 0 | #N/A
Last row with y2 data |  |  | #N/A |  | 38 | 3040.00 | #N/A | #N/A | #N/A | #N/A | #N/A | #N/A | #N/A |  |  |  |  |  |  |  | #N/A | #N/A | #N/A |  | #N/A | #N/A | #N/A |  |  | 0.00 | 0.00 |  |  | 0.00 | 0 | #N/A
Last row with paired 2nd set data |  |  | #N/A |  | 39 | 3120.00 | #N/A | #N/A | #N/A | #N/A | #N/A | #N/A | #N/A |  |  |  |  |  |  |  | #N/A | #N/A | #N/A |  | #N/A | #N/A | #N/A |  |  | 0.00 | 0.00 |  |  | 0.00 | 0 | #N/A
First row with x2 data |  |  | #N/A |  | 40 | 3200.00 | #N/A | #N/A | #N/A | #N/A | #N/A | #N/A | #N/A |  |  |  |  |  |  |  | #N/A | #N/A | #N/A |  | #N/A | #N/A | #N/A |  |  | 0.00 | 0.00 |  |  | 0.00 | 0 | #N/A
First row with y2 data |  |  | #N/A |  | 41 | 3280.00 | #N/A | #N/A | #N/A | #N/A | #N/A | #N/A | #N/A |  |  |  |  |  |  |  | #N/A | #N/A | #N/A |  | #N/A | #N/A | #N/A |  |  | 0.00 | 0.00 |  |  | 0.00 | 0 | #N/A
First row with paired 2nd set data |  |  | #N/A |  | 42 | 3360.00 | #N/A | #N/A | #N/A | #N/A | #N/A | #N/A | #N/A |  |  |  |  |  |  |  | #N/A | #N/A | #N/A |  | #N/A | #N/A | #N/A |  |  | 0.00 | 0.00 |  |  | 0.00 | 0 | #N/A
 |  |  |  |  | 43 | 3440.00 | #N/A | #N/A | #N/A | #N/A | #N/A | #N/A | #N/A |  |  |  |  |  |  |  | #N/A | #N/A | #N/A |  | #N/A | #N/A | #N/A |  |  | 0.00 | 0.00 |  |  | 0.00 | 0 | #N/A
 |  |  |  |  | 44 | 3520.00 | #N/A | #N/A | #N/A | #N/A | #N/A | #N/A | #N/A |  |  |  |  |  |  |  | #N/A | #N/A | #N/A |  | #N/A | #N/A | #N/A |  |  | 0.00 | 0.00 |  |  | 0.00 | 0 | #N/A
fit for the first dataset |  |  |  |  | 45 | 3600.00 | #N/A | #N/A | #N/A | #N/A | #N/A | #N/A | #N/A |  |  |  |  |  |  |  | #N/A | #N/A | #N/A |  | #N/A | #N/A | #N/A |  |  | 0.00 | 0.00 |  |  | 0.00 | 0 | #N/A
coeffs | #N/A |  |  |  | 46 | 3680.00 | #N/A | #N/A | #N/A | #N/A | #N/A | #N/A | #N/A |  |  |  |  |  |  |  | #N/A | #N/A | #N/A |  | #N/A | #N/A | #N/A |  |  | 0.00 | 0.00 |  |  | 0.00 | 0 | #N/A
unc. |  |  |  |  | 47 | 3760.00 | #N/A | #N/A | #N/A | #N/A | #N/A | #N/A | #N/A |  |  |  |  |  |  |  | #N/A | #N/A | #N/A |  | #N/A | #N/A | #N/A |  |  | 0.00 | 0.00 |  |  | 0.00 | 0 | #N/A
stats |  |  |  |  | 48 | 3840.00 | #N/A | #N/A | #N/A | #N/A | #N/A | #N/A | #N/A |  |  |  |  |  |  |  | #N/A | #N/A | #N/A |  | #N/A | #N/A | #N/A |  |  | 0.00 | 0.00 |  |  | 0.00 | 0 | #N/A
 |  |  |  |  | 49 | 3920.00 | #N/A | #N/A | #N/A | #N/A | #N/A | #N/A | #N/A |  |  |  |  |  |  |  | #N/A | #N/A | #N/A |  | #N/A | #N/A | #N/A |  |  | 0.00 | 0.00 |  |  | 0.00 | 0 | #N/A
 |  |  |  |  | 50 | 4000.00 | #N/A | #N/A | #N/A | #N/A | #N/A | #N/A | #N/A |  |  |  |  |  |  |  | #N/A | #N/A | #N/A |  | #N/A | #N/A | #N/A |  |  | 0.00 | 0.00 |  |  | 0.00 | 0 | #N/A
fit for the second dataset |  |  |  |  | 51 | 4080.00 | #N/A | #N/A | #N/A | #N/A | #N/A | #N/A | #N/A |  |  |  |  |  |  |  | #N/A | #N/A | #N/A |  | #N/A | #N/A | #N/A |  |  | 0.00 | 0.00 |  |  | 0.00 | 0 | #N/A
coeffs | #N/A |  |  |  | 52 | 4160.00 | #N/A | #N/A | #N/A | #N/A | #N/A | #N/A | #N/A |  |  |  |  |  |  |  | #N/A | #N/A | #N/A |  | #N/A | #N/A | #N/A |  |  | 0.00 | 0.00 |  |  | 0.00 | 0 | #N/A
unc. |  |  |  |  | 53 | 4240.00 | #N/A | #N/A | #N/A | #N/A | #N/A | #N/A | #N/A |  |  |  |  |  |  |  | #N/A | #N/A | #N/A |  | #N/A | #N/A | #N/A |  |  | 0.00 | 0.00 |  |  | 0.00 | 0 | #N/A
stats |  |  |  |  | 54 | 4320.00 | #N/A | #N/A | #N/A | #N/A | #N/A | #N/A | #N/A |  |  |  |  |  |  |  | #N/A | #N/A | #N/A |  | #N/A | #N/A | #N/A |  |  | 0.00 | 0.00 |  |  | 0.00 | 0 | #N/A
 |  |  |  |  | 55 | 4400.00 | #N/A | #N/A | #N/A | #N/A | #N/A | #N/A | #N/A |  |  |  |  |  |  |  | #N/A | #N/A | #N/A |  | #N/A | #N/A | #N/A |  |  | 0.00 | 0.00 |  |  | 0.00 | 0 | #N/A
 |  |  |  |  | 56 | 4480.00 | #N/A | #N/A | #N/A | #N/A | #N/A | #N/A | #N/A |  |  |  |  |  |  |  | #N/A | #N/A | #N/A |  | #N/A | #N/A | #N/A |  |  | 0.00 | 0.00 |  |  | 0.00 | 0 | #N/A
Final row with data in x-data column (N) |  |  |  |  | 57 | 4560.00 | #N/A | #N/A | #N/A | #N/A | #N/A | #N/A | #N/A |  |  |  |  |  |  |  | #N/A | #N/A | #N/A |  | #N/A | #N/A | #N/A |  |  | 0.00 | 0.00 |  |  | 0.00 | 0 | #N/A
36 |  |  |  |  | 58 | 4640.00 | #N/A | #N/A | #N/A | #N/A | #N/A | #N/A | #N/A |  |  |  |  |  |  |  | #N/A | #N/A | #N/A |  | #N/A | #N/A | #N/A |  |  | 0.00 | 0.00 |  |  | 0.00 | 0 | #N/A
 |  |  |  |  | 59 | 4720.00 | #N/A | #N/A | #N/A | #N/A | #N/A | #N/A | #N/A |  |  |  |  |  |  |  | #N/A | #N/A | #N/A |  | #N/A | #N/A | #N/A |  |  | 0.00 | 0.00 |  |  | 0.00 | 0 | #N/A
 | Manual fit info |  |  |  | 60 | 4800.00 | #N/A | #N/A | #N/A | #N/A | #N/A | #N/A | #N/A |  |  |  |  |  |  |  | #N/A | #N/A | #N/A |  | #N/A | #N/A | #N/A |  |  | 0.00 | 0.00 |  |  | 0.00 | 0 | #N/A
Last row with x data |  |  | #N/A |  | 61 | 4880.00 | #N/A | #N/A | #N/A | #N/A | #N/A | #N/A | #N/A |  |  |  |  |  |  |  | #N/A | #N/A | #N/A |  | #N/A | #N/A | #N/A |  |  | 0.00 | 0.00 |  |  | 0.00 | 0 | #N/A
Last row with y data |  |  | #N/A |  | 62 | 4960.00 | #N/A | #N/A | #N/A | #N/A | #N/A | #N/A | #N/A |  |  |  |  |  |  |  | #N/A | #N/A | #N/A |  | #N/A | #N/A | #N/A |  |  | 0.00 | 0.00 |  |  | 0.00 | 0 | #N/A
Last row with paired data |  |  | #N/A |  | 63 | 5040.00 | #N/A | #N/A | #N/A | #N/A | #N/A | #N/A | #N/A |  |  |  |  |  |  |  | #N/A | #N/A | #N/A |  | #N/A | #N/A | #N/A |  |  | 0.00 | 0.00 |  |  | 0.00 | 0 | #N/A
First row with x data |  |  | #N/A |  | 64 | 5120.00 | #N/A | #N/A | #N/A | #N/A | #N/A | #N/A | #N/A |  |  |  |  |  |  |  | #N/A | #N/A | #N/A |  | #N/A | #N/A | #N/A |  |  | 0.00 | 0.00 |  |  | 0.00 | 0 | #N/A
First row with y data |  |  | #N/A |  | 65 | 5200.00 | #N/A | #N/A | #N/A | #N/A | #N/A | #N/A | #N/A |  |  |  |  |  |  |  | #N/A | #N/A | #N/A |  | #N/A | #N/A | #N/A |  |  | 0.00 | 0.00 |  |  | 0.00 | 0 | #N/A
First row with paired data |  |  | #N/A |  | 66 | 5280.00 | #N/A | #N/A | #N/A | #N/A | #N/A | #N/A | #N/A |  |  |  |  |  |  |  | #N/A | #N/A | #N/A |  | #N/A | #N/A | #N/A |  |  | 0.00 | 0.00 |  |  | 0.00 | 0 | #N/A
 |  |  |  |  | 67 | 5360.00 | #N/A | #N/A | #N/A | #N/A | #N/A | #N/A | #N/A |  |  |  |  |  |  |  | #N/A | #N/A | #N/A |  | #N/A | #N/A | #N/A |  |  | 0.00 | 0.00 |  |  | 0.00 | 0 | #N/A
 |  |  |  |  | 68 | 5440.00 | #N/A | #N/A | #N/A | #N/A | #N/A | #N/A | #N/A |  |  |  |  |  |  |  | #N/A | #N/A | #N/A |  | #N/A | #N/A | #N/A |  |  | 0.00 | 0.00 |  |  | 0.00 | 0 | #N/A
 |  |  |  |  | 69 | 5520.00 | #N/A | #N/A | #N/A | #N/A | #N/A | #N/A | #N/A |  |  |  |  |  |  |  | #N/A | #N/A | #N/A |  | #N/A | #N/A | #N/A |  |  | 0.00 | 0.00 |  |  | 0.00 | 0 | #N/A
 |  |  |  |  | 70 | 5600.00 | #N/A | #N/A | #N/A | #N/A | #N/A | #N/A | #N/A |  |  |  |  |  |  |  | #N/A | #N/A | #N/A |  | #N/A | #N/A | #N/A |  |  | 0.00 | 0.00 |  |  | 0.00 | 0 | #N/A
 |  |  |  |  | 71 | 5680.00 | #N/A | #N/A | #N/A | #N/A | #N/A | #N/A | #N/A |  |  |  |  |  |  |  | #N/A | #N/A | #N/A |  | #N/A | #N/A | #N/A |  |  | 0.00 | 0.00 |  |  | 0.00 | 0 | #N/A
 |  |  |  |  | 72 | 5760.00 | #N/A | #N/A | #N/A | #N/A | #N/A | #N/A | #N/A |  |  |  |  |  |  |  | #N/A | #N/A | #N/A |  | #N/A | #N/A | #N/A |  |  | 0.00 | 0.00 |  |  | 0.00 | 0 | #N/A
 |  |  |  |  | 73 | 5840.00 | #N/A | #N/A | #N/A | #N/A | #N/A | #N/A | #N/A |  |  |  |  |  |  |  | #N/A | #N/A | #N/A |  | #N/A | #N/A | #N/A |  |  | 0.00 | 0.00 |  |  | 0.00 | 0 | #N/A
 |  |  |  |  | 74 | 5920.00 | #N/A | #N/A | #N/A | #N/A | #N/A | #N/A | #N/A |  |  |  |  |  |  |  | #N/A | #N/A | #N/A |  | #N/A | #N/A | #N/A |  |  | 0.00 | 0.00 |  |  | 0.00 | 0 | #N/A
 |  |  |  |  | 75 | 6000.00 | #N/A | #N/A | #N/A | #N/A | #N/A | #N/A | #N/A |  |  |  |  |  |  |  | #N/A | #N/A | #N/A |  | #N/A | #N/A | #N/A |  |  | 0.00 | 0.00 |  |  | 0.00 | 0 | #N/A
 |  |  |  |  | 76 | 6080.00 | #N/A | #N/A | #N/A | #N/A | #N/A | #N/A | #N/A |  |  |  |  |  |  |  | #N/A | #N/A | #N/A |  | #N/A | #N/A | #N/A |  |  | 0.00 | 0.00 |  |  | 0.00 | 0 | #N/A
 |  |  |  |  | 77 | 6160.00 | #N/A | #N/A | #N/A | #N/A | #N/A | #N/A | #N/A |  |  |  |  |  |  |  | #N/A | #N/A | #N/A |  | #N/A | #N/A | #N/A |  |  | 0.00 | 0.00 |  |  | 0.00 | 0 | #N/A
 |  |  |  |  | 78 | 6240.00 | #N/A | #N/A | #N/A | #N/A | #N/A | #N/A | #N/A |  |  |  |  |  |  |  | #N/A | #N/A | #N/A |  | #N/A | #N/A | #N/A |  |  | 0.00 | 0.00 |  |  | 0.00 | 0 | #N/A
 |  |  |  |  | 79 | 6320.00 | #N/A | #N/A | #N/A | #N/A | #N/A | #N/A | #N/A |  |  |  |  |  |  |  | #N/A | #N/A | #N/A |  | #N/A | #N/A | #N/A |  |  | 0.00 | 0.00 |  |  | 0.00 | 0 | #N/A
 |  |  |  |  | 80 | 6400.00 | #N/A | #N/A | #N/A | #N/A | #N/A | #N/A | #N/A |  |  |  |  |  |  |  | #N/A | #N/A | #N/A |  | #N/A | #N/A | #N/A |  |  | 0.00 | 0.00 |  |  | 0.00 | 0 | #N/A
 |  |  |  |  | 81 | 6480.00 | #N/A | #N/A | #N/A | #N/A | #N/A | #N/A | #N/A |  |  |  |  |  |  |  | #N/A | #N/A | #N/A |  | #N/A | #N/A | #N/A |  |  | 0.00 | 0.00 |  |  | 0.00 | 0 | #N/A
 |  |  |  |  | 82 | 6560.00 | #N/A | #N/A | #N/A | #N/A | #N/A | #N/A | #N/A |  |  |  |  |  |  |  | #N/A | #N/A | #N/A |  | #N/A | #N/A | #N/A |  |  | 0.00 | 0.00 |  |  | 0.00 | 0 | #N/A
 |  |  |  |  | 83 | 6640.00 | #N/A | #N/A | #N/A | #N/A | #N/A | #N/A | #N/A |  |  |  |  |  |  |  | #N/A | #N/A | #N/A |  | #N/A | #N/A | #N/A |  |  | 0.00 | 0.00 |  |  | 0.00 | 0 | #N/A
 |  |  |  |  | 84 | 6720.00 | #N/A | #N/A | #N/A | #N/A | #N/A | #N/A | #N/A |  |  |  |  |  |  |  | #N/A | #N/A | #N/A |  | #N/A | #N/A | #N/A |  |  | 0.00 | 0.00 |  |  | 0.00 | 0 | #N/A
 |  |  |  |  | 85 | 6800.00 | #N/A | #N/A | #N/A | #N/A | #N/A | #N/A | #N/A |  |  |  |  |  |  |  | #N/A | #N/A | #N/A |  | #N/A | #N/A | #N/A |  |  | 0.00 | 0.00 |  |  | 0.00 | 0 | #N/A
 |  |  |  |  | 86 | 6880.00 | #N/A | #N/A | #N/A | #N/A | #N/A | #N/A | #N/A |  |  |  |  |  |  |  | #N/A | #N/A | #N/A |  | #N/A | #N/A | #N/A |  |  | 0.00 | 0.00 |  |  | 0.00 | 0 | #N/A
 |  |  |  |  | 87 | 6960.00 | #N/A | #N/A | #N/A | #N/A | #N/A | #N/A | #N/A |  |  |  |  |  |  |  | #N/A | #N/A | #N/A |  | #N/A | #N/A | #N/A |  |  | 0.00 | 0.00 |  |  | 0.00 | 0 | #N/A
 |  |  |  |  | 88 | 7040.00 | #N/A | #N/A | #N/A | #N/A | #N/A | #N/A | #N/A |  |  |  |  |  |  |  | #N/A | #N/A | #N/A |  | #N/A | #N/A | #N/A |  |  | 0.00 | 0.00 |  |  | 0.00 | 0 | #N/A
 |  |  |  |  | 89 | 7120.00 | #N/A | #N/A | #N/A | #N/A | #N/A | #N/A | #N/A |  |  |  |  |  |  |  | #N/A | #N/A | #N/A |  | #N/A | #N/A | #N/A |  |  | 0.00 | 0.00 |  |  | 0.00 | 0 | #N/A
 |  |  |  |  | 90 | 7200.00 | #N/A | #N/A | #N/A | #N/A | #N/A | #N/A | #N/A |  |  |  |  |  |  |  | #N/A | #N/A | #N/A |  | #N/A | #N/A | #N/A |  |  | 0.00 | 0.00 |  |  | 0.00 | 0 | #N/A
 |  |  |  |  | 91 | 7280.00 | #N/A | #N/A | #N/A | #N/A | #N/A | #N/A | #N/A |  |  |  |  |  |  |  | #N/A | #N/A | #N/A |  | #N/A | #N/A | #N/A |  |  | 0.00 | 0.00 |  |  | 0.00 | 0 | #N/A
 |  |  |  |  | 92 | 7360.00 | #N/A | #N/A | #N/A | #N/A | #N/A | #N/A | #N/A |  |  |  |  |  |  |  | #N/A | #N/A | #N/A |  | #N/A | #N/A | #N/A |  |  | 0.00 | 0.00 |  |  | 0.00 | 0 | #N/A
 |  |  |  |  | 93 | 7440.00 | #N/A | #N/A | #N/A | #N/A | #N/A | #N/A | #N/A |  |  |  |  |  |  |  | #N/A | #N/A | #N/A |  | #N/A | #N/A | #N/A |  |  | 0.00 | 0.00 |  |  | 0.00 | 0 | #N/A
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

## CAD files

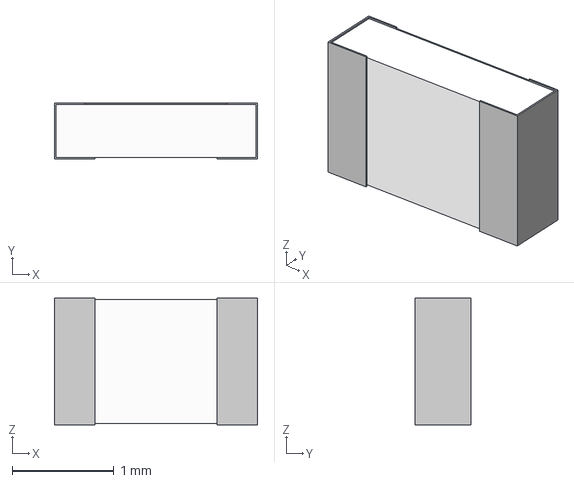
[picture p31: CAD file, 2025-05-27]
Revision01/Hardware/Amplifier/Altium/AltiumLL/Temp/RNCS0805BKE100K.stp
2.00 x 0.55 x 1.25 mm

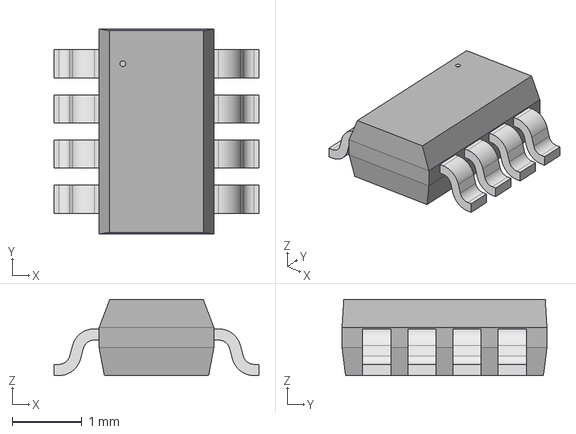
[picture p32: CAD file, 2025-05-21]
Revision01/Hardware/Amplifier/Altium/Imports/TLV9062IDDFR/AltiumDesigner/SOT_62IDDFR_TEX.step
2.95 x 2.95 x 1.09 mm

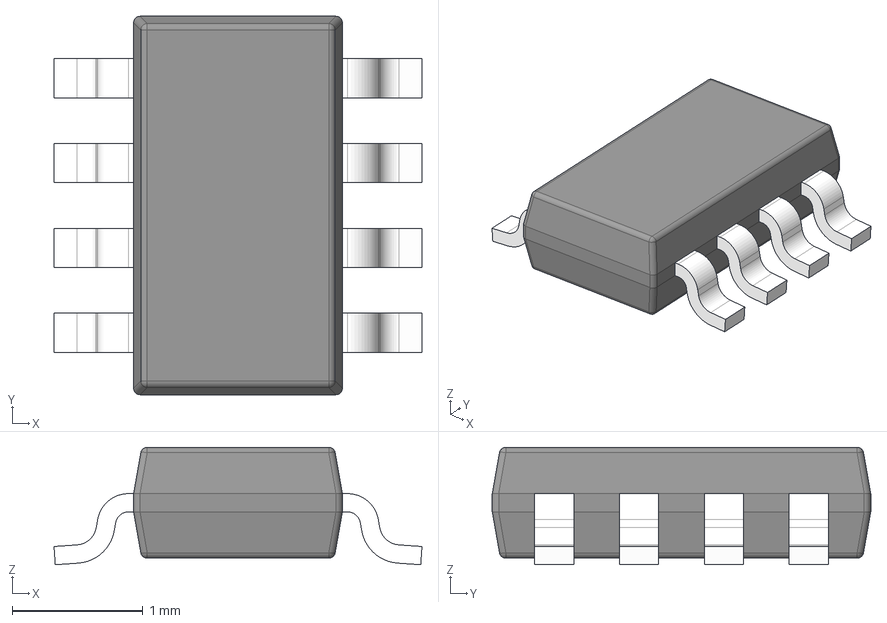
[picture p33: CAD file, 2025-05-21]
Revision01/Hardware/Amplifier/Altium/Imports/TLV9062IDDFR/DDF0008A.stp
2.82 x 2.90 x 0.9 mm
BODY-SO
LEAD-SO x 8
PIN1-ID

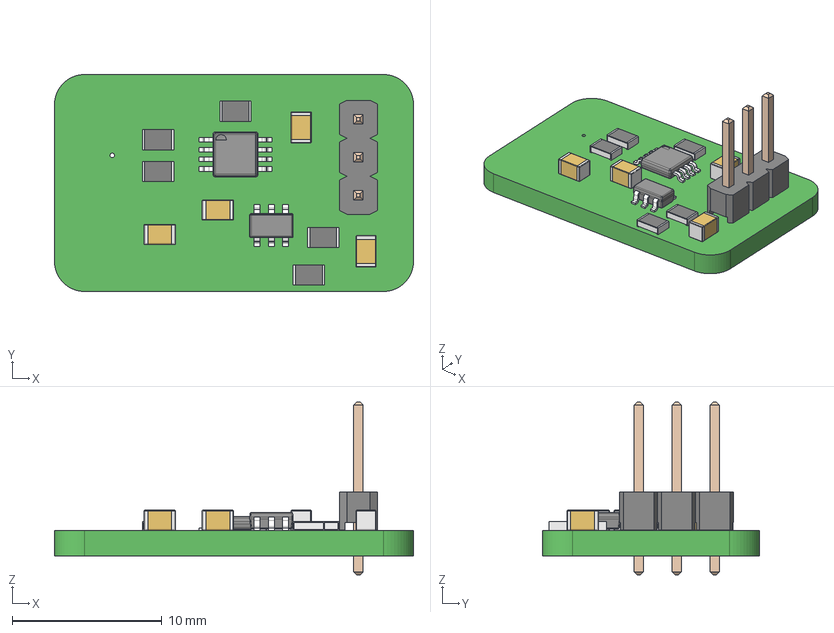
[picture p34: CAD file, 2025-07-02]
Revision01/Hardware/Amplifier/Altium/PCB1_AmplifierBoard.step
24.0 x 14.5 x 11.5 mm
6130xx11121_PIN x 3
Mid Body x 5
Mark x 5
BODY_MUY08A
LEAD_MUY08A x 8
EXP_PAD_MUY08A
BODY-SOT
LEAD-SOT x 6

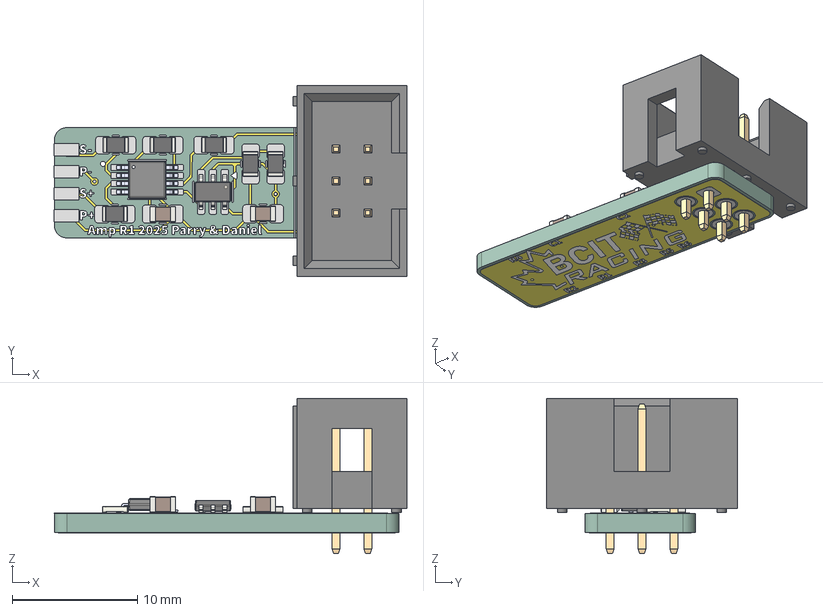
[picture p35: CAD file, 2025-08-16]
Revision01/Hardware/Product_2025-08-16/Amplifier/Amplifier.step
28.1 x 15.2 x 12.4 mm
C_0805_2012Metric x 2
kicad_embedded_3ADF6B6589A85DEB7AFC18F47F5DE8FC
R_0805_2012Metric x 6
TSOT-23-6
Amplifier_copper
Amplifier_pad
Amplifier_via
Amplifier_silkscreen
Amplifier_PCB

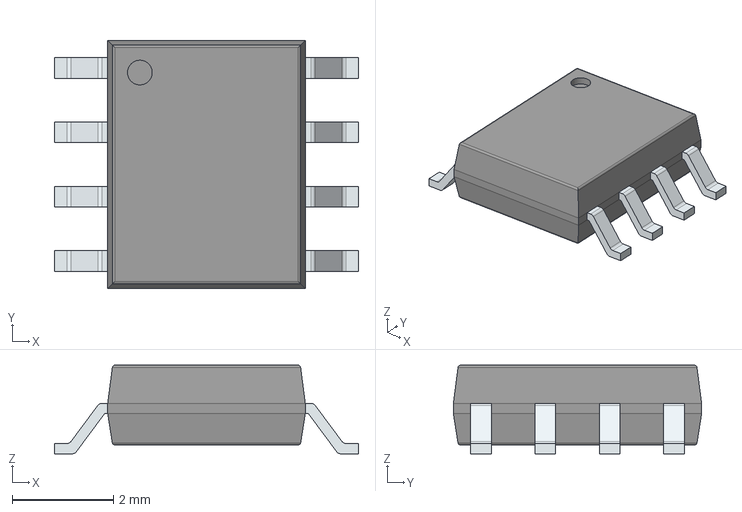
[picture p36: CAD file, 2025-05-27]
Revision01/Hardware/Amplifier/Altium/AltiumLL/Temp/NE555DR.stp
6.00 x 4.90 x 1.75 mm
PinsArrayLR

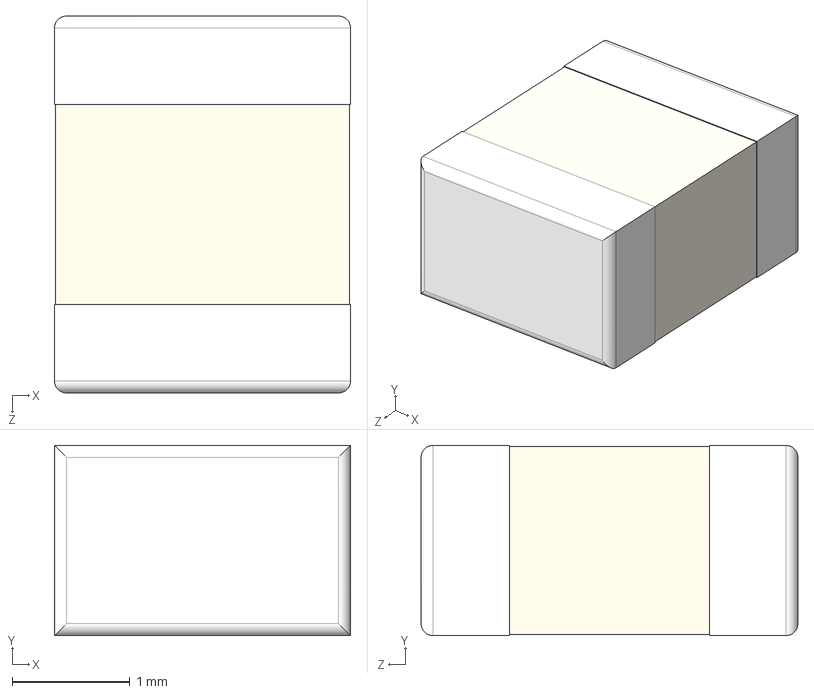
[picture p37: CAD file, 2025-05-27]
Revision01/Hardware/Amplifier/Altium/AltiumLL/Temp/B59807A0090A062.stp
2.51 x 1.61 x 3.20 mm

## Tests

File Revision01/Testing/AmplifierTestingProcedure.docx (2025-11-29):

# Amplifier board bring up

## Equipment

AD2

### TEST 1: Does the board work as intended?

1. Apply 5V across power rails.
2. Measure and record offset voltage
  a. Expected offset voltage: 1.66V
3. Vary (strainD+, strainD-) Record output voltage
  a. 5mV - expected
  b. -5mV – expected
4. Input sin wave (100Hz (-15mV,15mV) need to check that this range will not possibly break board)
  a. Expected output ranges from (100mV,3.10V) – just a quick guess

### TEST 2: Stimulating with realistic electrical conditions

1. Determine length of wire expected to be wired from sensor-amplifier to hub
2. Determine expected voltage level provided by HUB, and apply that voltage to power amplifiers across wire length
3. Determine the expected differential strain voltage levels corresponding to 8000lb’s
4. Measure power rails
  a. Note any significant variation amongst boards
5. Apply strain voltages between at the determined differential strain voltage level.

### TEST 3: Stimulating realistic mechanical conditions – may or may not be run depending on test difficulty.

1. Given the realistic voltage and wire conditions.
2. Apply 8000lb’s of force and measure the signal.

There is a chance that there are significant variations amongst the board that each sensor will be individually calibrated. Things like temperature could even affect it.

(OFFSET, GAIN)

# CALIBRATION SEQUENCE

To calibrate it. We need to know precisely how the voltage across strain gauge is correlated with strain.

# Test algorithm(DC, SIN, STEP, FREQ)

1. Apply V_(in) = 0V
2. Measure V_(in) scope
3. Apply sin wave of certain range at 10Hz – (-10mV,10mV)
4. Measure V_(in) scope
5. Measure frequency response: (-10mV,10mV), (1Hz-10KHz)
6. Measure slew-rate apply 10mV at 10Hz square wave -> measure output. Use (dv)/(dt) of output

Use perf boards, attach pogo pins to it. Then run stimulations.

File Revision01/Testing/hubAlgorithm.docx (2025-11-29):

# Algorithm for HUB

1. TURN ON MOSFET
2. MEASURE 8 STRAIN GAUGES after X time
3. TURN OFF MOSFET
4. MEASURE IMU DATA
5. TRANSMIT DATA

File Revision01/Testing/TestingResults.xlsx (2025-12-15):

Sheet: Sheet1
Testing procedure
Testing 5V rail | Expected(V) | Board 1
strain connector 5V | 5 | 5
TLV9061-Q1 | 5 | 5
INA333 | 5 | 5
Testing OFFSET
Resistor voltage divider | 1.67 | 1.67
Buffer output | 1.67 | 1.67
Measuring INA333 output
Input 0V differential | 1.67 | 1.67
1HZ Sin wave MAX 15mV differential(2.5V offset) | 3.1 | 3.191
1Hz Sin wave MIN Input - 15mV differential (2.5V offset) | 0.1 | 0.1578
Attach real strain gauge test
offset voltage(V) | 1.67 | 1.444
output voltage(V) | 1.67 | 1.47
Attach strainGauge 0lbs of force
Get linear response for force applied

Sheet: Screenshot
Test setup
INPUT | SCOPE MEASUREMENT OF INPUT
BOARD 1
1Hz |  | 10Hz |  | 100Hz | 1K Hz
 |  |  |  |  |  | x
BOARD 2
1Hz
 |  |  | 100Hz

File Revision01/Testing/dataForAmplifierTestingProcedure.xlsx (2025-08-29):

Parameters to measure
Offset voltage
GAIN
Slew rate
resolution
magnitude and phase response
 | StrainDifferential(mV)
 | 100Hz sin wave (-10mV,10mV)

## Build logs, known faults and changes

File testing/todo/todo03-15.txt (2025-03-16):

add test points for power-rails and comm ports
add power switch with integrated LED
replace load switch with mosfet
add series and pull-ups on SPI bus(open drain)
choose and add in capacitor at differential strain gauge voltage(maybe)
choose and add capacitor near strain gauge VCC
choose battery holder, put specification of batteries in kicad
change load switch to mosfet
add mosfet switch to every sensor

Goals for today:

choose mosfets to switching
choose capacitors for VCC_strain gauge

Result - By 03-16

Both mosfet will not be added into circuit. Both IMU and ANTENNA have sleep mode, which is in the micro to milliamp current usage range. Add in
capacitor will optimize the system slighty, however the complexity of the problem is high. So I have opted to accept the uncertainty of the measurements.

Capacitor. Placement of capacitor is not accross differential. But we need 1 cap for each AIN, in addition to this, our switching frequency
will be varied significantly due to our battery range. This is very complicated stuff to size for. So in terms of time, it may be best to not add this in.

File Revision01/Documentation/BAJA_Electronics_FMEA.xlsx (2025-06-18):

Item | Function | Failure Mode | Failure Effect | Severity | Cause | Occurrence | Current Controls | Detection | RPN | Recommended Action
5V Voltage Regulator | Overheating / thermal shutdown | other components get overly heated | Components break due to excessive heat | 10 | inefficient use of power | 8 | none | 10 | 800 | STM32 nucleo has built-in temperature sensor Or we can use a buck-convertor to not lose heat.
Strain Gauge Wiring | Transmit strain signal | Open circuit or noise pickup | Incorrect strain readings | 7 | Connector failure, EMI, vibration | 3 | amplifier board | 6 | 168
Amplifier board | Amplifies small signal of strain | reduces effect of noise onto wires, provides stability | less accurate readings | 8 | unstable mounting | 9 | Capacitors, and RC filters. | 5 | 360 | Talk with johnny to see how mechanicals manages this issue
 |  |  |  |  |  |  |  |  | 0
Buck convertor | Steps voltage down to 5.5V for energy efficiency, and to manage heat dissipation | Significant EMI can be generated | Cross talk between Analog traces | 3 | poorly routed traces | 4 | Lots of capacitors, amplifier board | 7 | 84
Buck convertor | wired incorrectly or soldered incorrectly | Does not properly regulate voltage | No voltage goes through to output | 10 | design mistake, poor soldering | 7 | 0 ohm resistor to bypass buck, test point | 2 | 140 | read datasheet in more detail to determine more options

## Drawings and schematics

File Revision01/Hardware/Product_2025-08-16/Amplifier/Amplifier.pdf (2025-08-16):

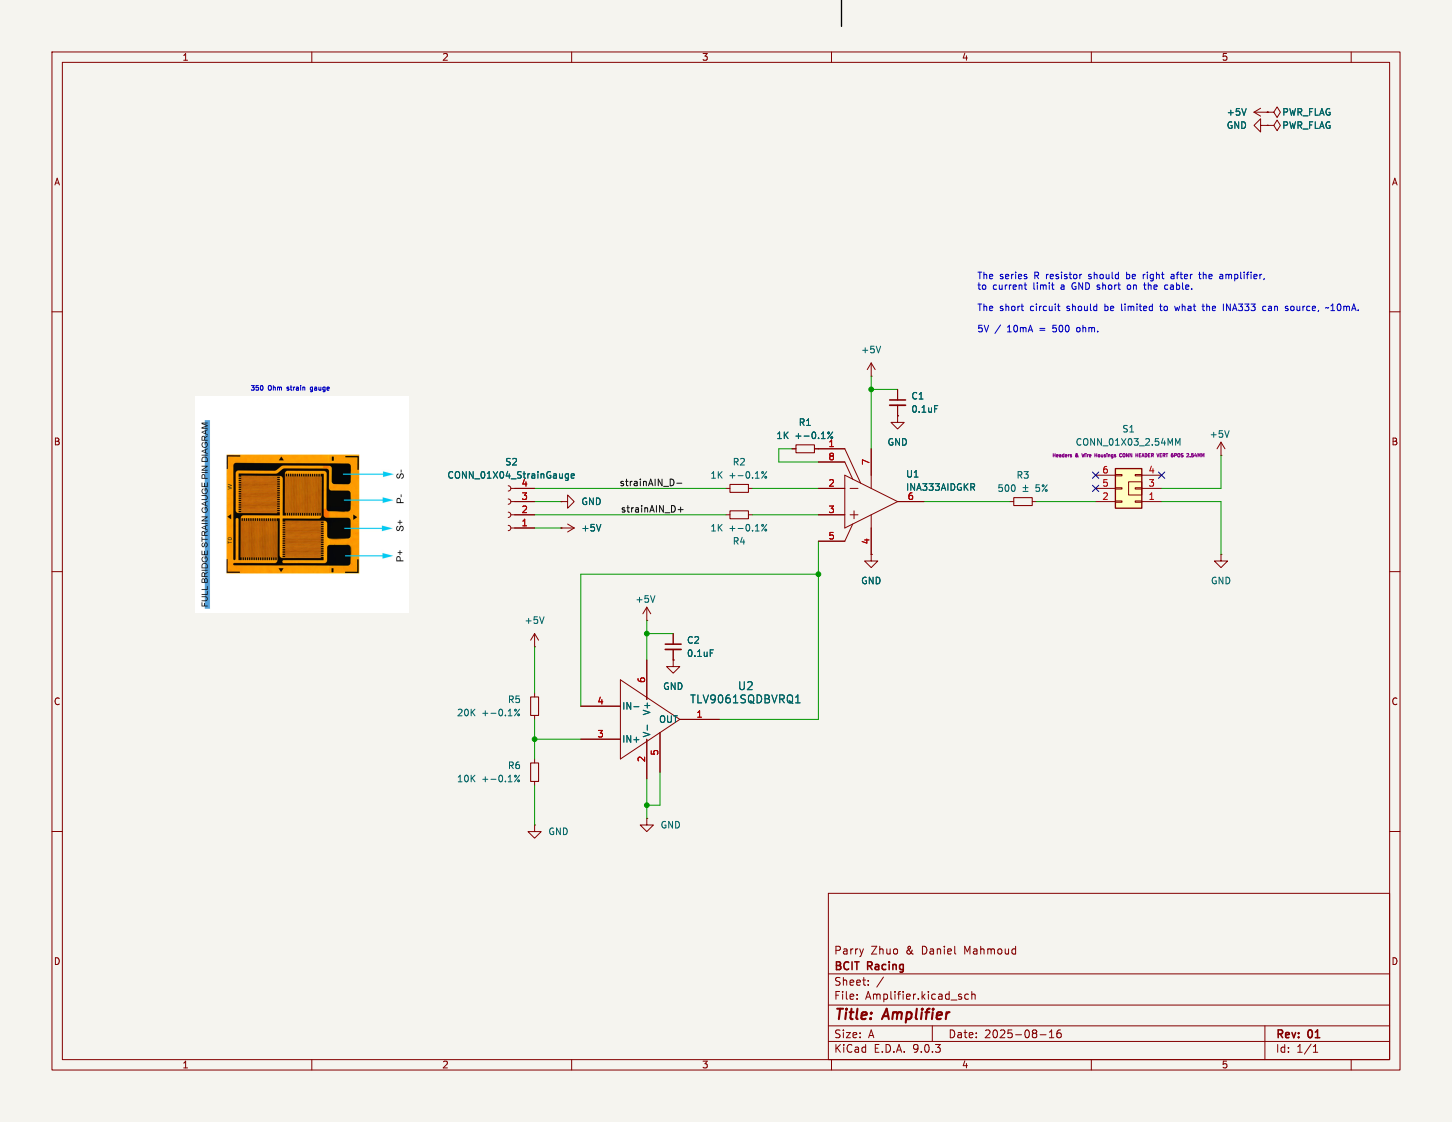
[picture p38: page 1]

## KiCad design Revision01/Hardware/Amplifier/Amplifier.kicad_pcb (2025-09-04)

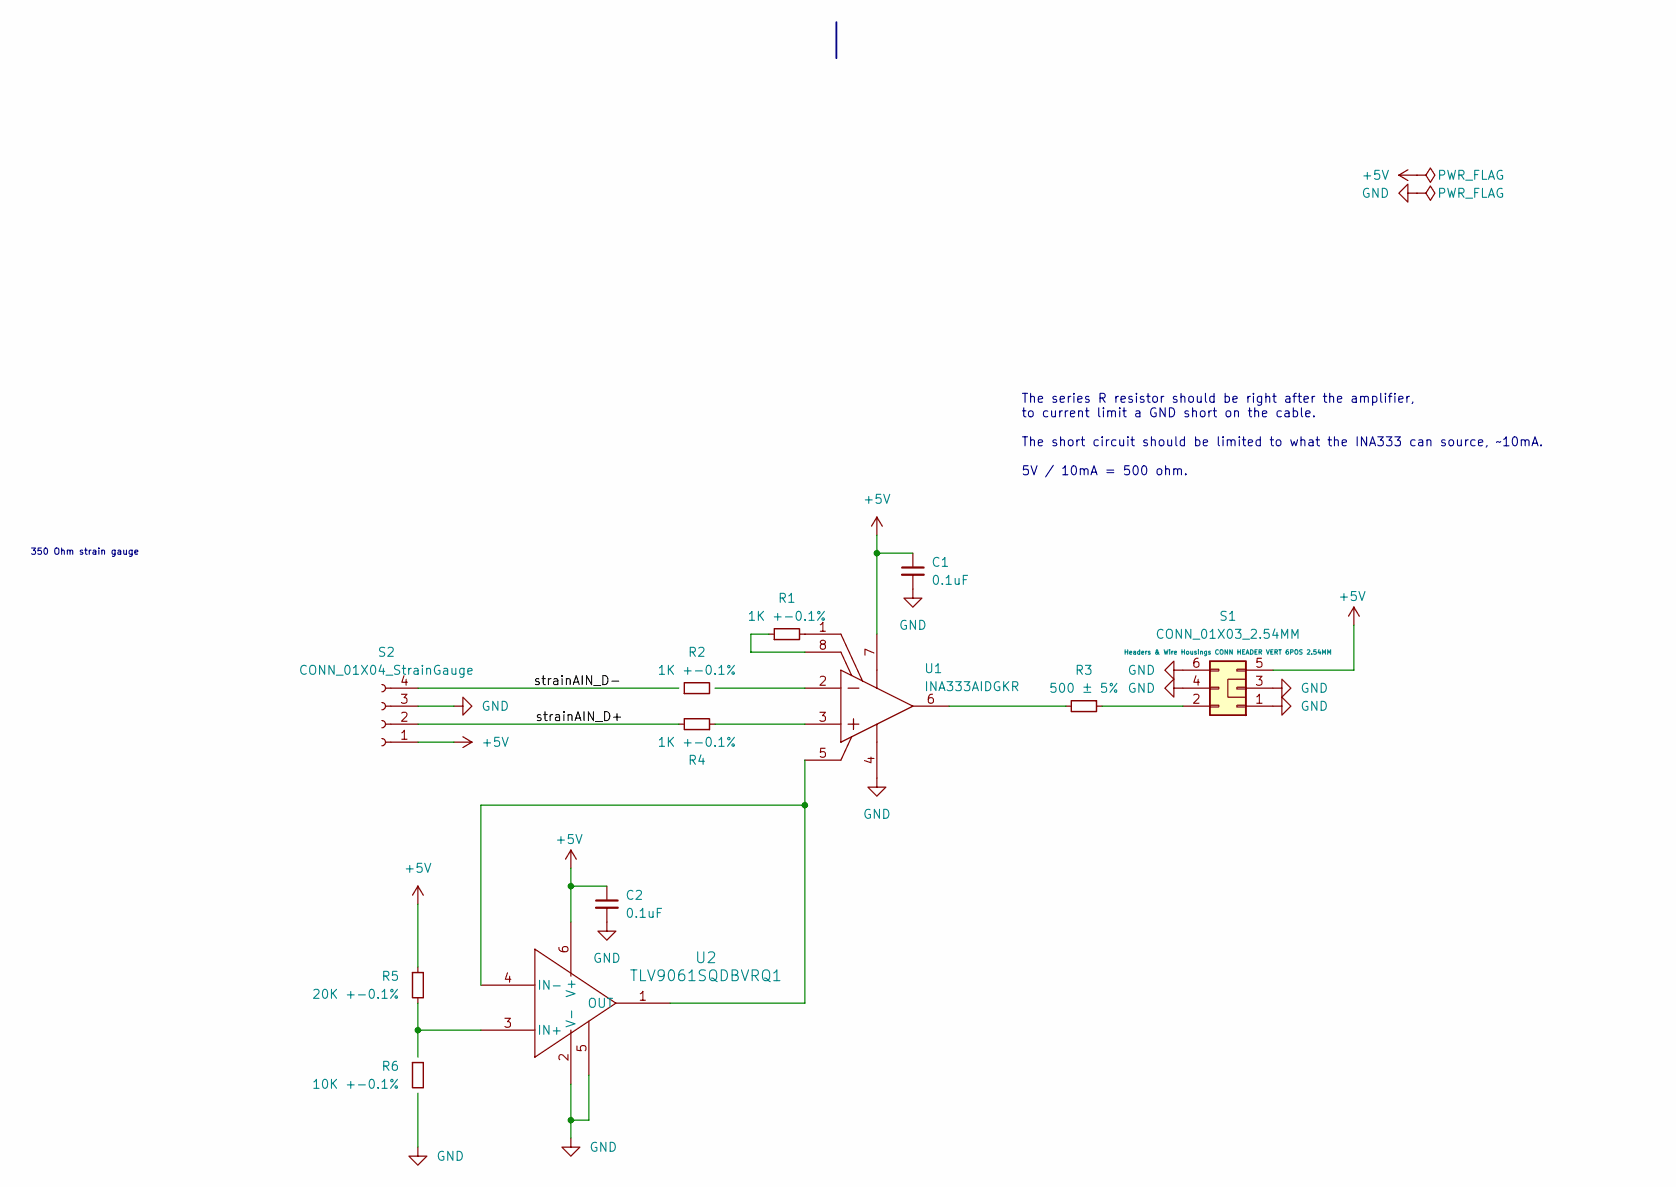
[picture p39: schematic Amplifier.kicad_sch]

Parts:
C1, C2: 0.1uF; C_0805_2012Metric_Pad1.18x1.45mm_HandSolder; Manufacturer Part Number CL21B104KBCNNWC; Mouser Part Number 187-CL21B104KBCNNWC
R1, R2, R4: 1K +-0.1%; R_0805_2012Metric_Pad1.20x1.40mm_HandSolder; Manufacturer Part Number MCU08050D1001BP500; Mouser Part Number 594-MCU0805D1001BP5
R3: 500 ± 5%; R_0805_2012Metric_Pad1.20x1.40mm_HandSolder; Manufacturer Part Number MCU0805MD4990DP500; Mouser Part Number 594-MCU0805MD4990DP5
R5: 20K +-0.1%; R_0805_2012Metric_Pad1.20x1.40mm_HandSolder; Manufacturer Part Number RG2012P-203-B-T5; Mouser Part Number 754-RG2012P-203-B-T5
R6: 10K +-0.1%; R_0805_2012Metric_Pad1.20x1.40mm_HandSolder; Manufacturer Part Number RG2012P-103-B-T5; Mouser Part Number 754-RG2012P-103-B-T5
S1: CONN_01X03_2.54MM; AdamTech_BHR-06-VUA; Manufacturer Part Number BHR-06-VUA; Mouser Part Number 737-BHR-06-VUA
S2: CONN_01X04_StrainGauge; CONN_01X04
U1: INA333AIDGKR; INA333AIDGKR_SOP65P490X110-8N; Manufacturer Part Number INA333AIDGKR; Mouser Part Number 595-INA333AIDGKR
U2: TLV9061SQDBVRQ1; TSOT-23-6; Manufacturer Part Number TLV9061SQDBVRQ1; Mouser Part Number 595-TLV9061SQDBVRQ1

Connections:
+5V: C1.1, C2.1, R5.1, S1.5, S2.1, U1.7 (V+), U2.6 (V+)
/strainAIN_D+: R4.2, S2.2
/strainAIN_D-: R2.1, S2.4
GND: C1.2, C2.2, R6.2, S1.1, S1.3, S1.4, S1.6, S2.3, U1.4 (V-), U2.2 (V-), U2.5
unnamed: R1.1, U1.8 (RG)
unnamed: R1.2, U1.1 (RG)
unnamed: R3.1, S1.2
unnamed: U1.5 (REF), U2.1 (OUT), U2.4 (IN-)
unnamed: R4.1, U1.3 (VIN+)
unnamed: R2.2, U1.2 (VIN-)
unnamed: R3.2, U1.6 (VOUT)
unnamed: R5.2, R6.1, U2.3 (IN+)

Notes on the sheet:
350 Ohm strain gauge
The series R resistor should be right after the amplifier, to current limit a GND short on the cable. The short circuit should be limited to what the INA333 can source, ~10mA. 5V / 10mA = 500 ohm.

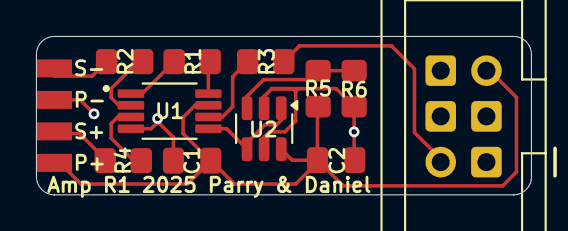
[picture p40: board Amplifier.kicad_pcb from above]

Board: 2 copper layers, 27.5 x 8.8 mm, 12 parts (0 on the bottom side), 12 nets.

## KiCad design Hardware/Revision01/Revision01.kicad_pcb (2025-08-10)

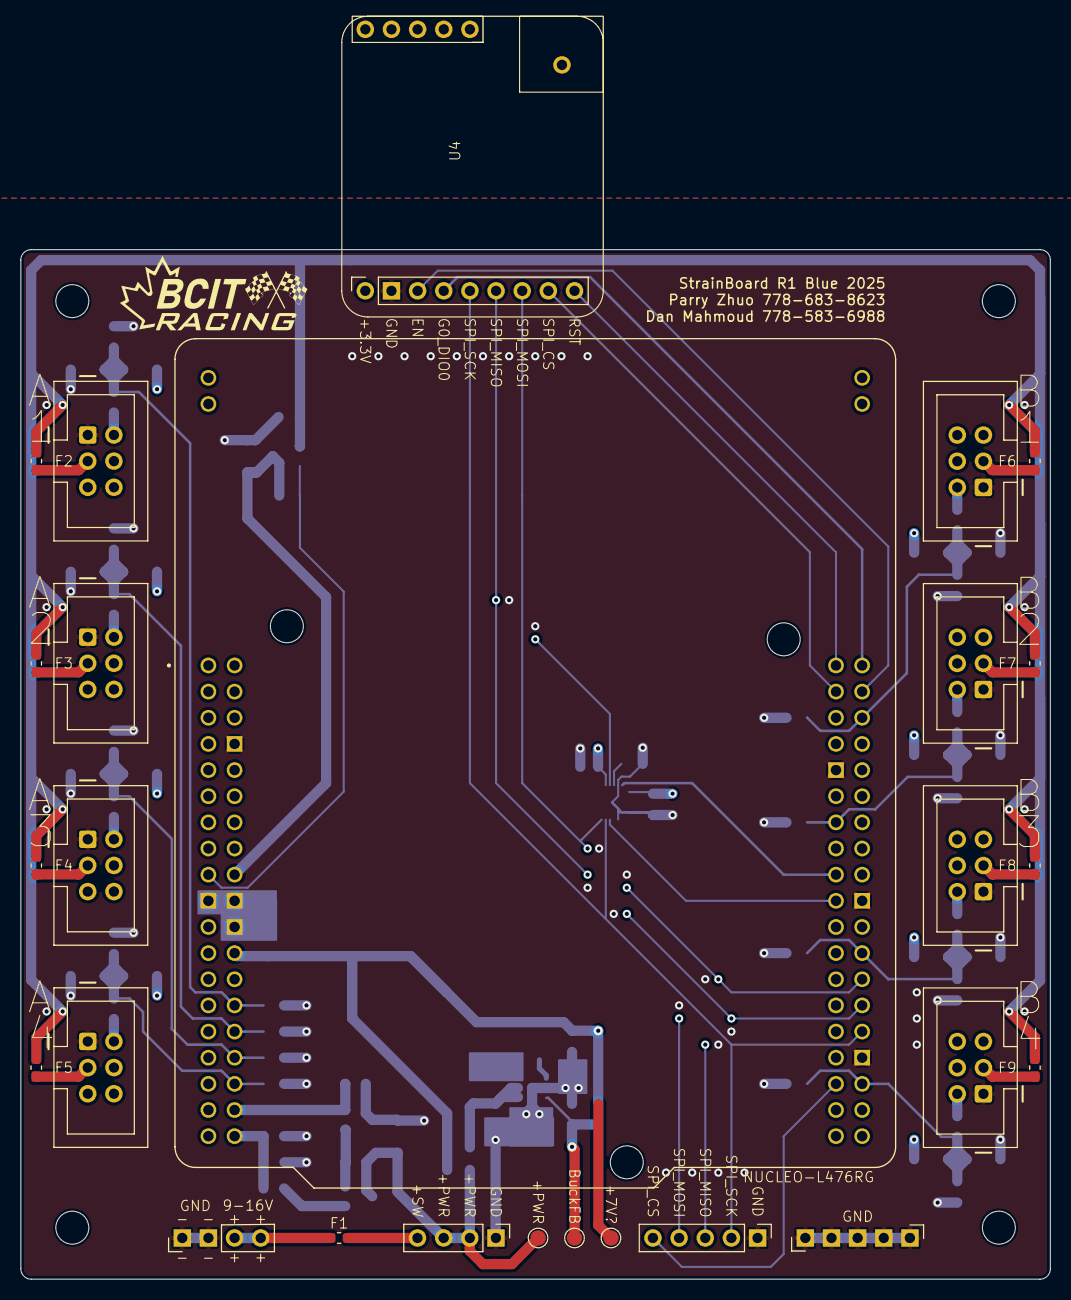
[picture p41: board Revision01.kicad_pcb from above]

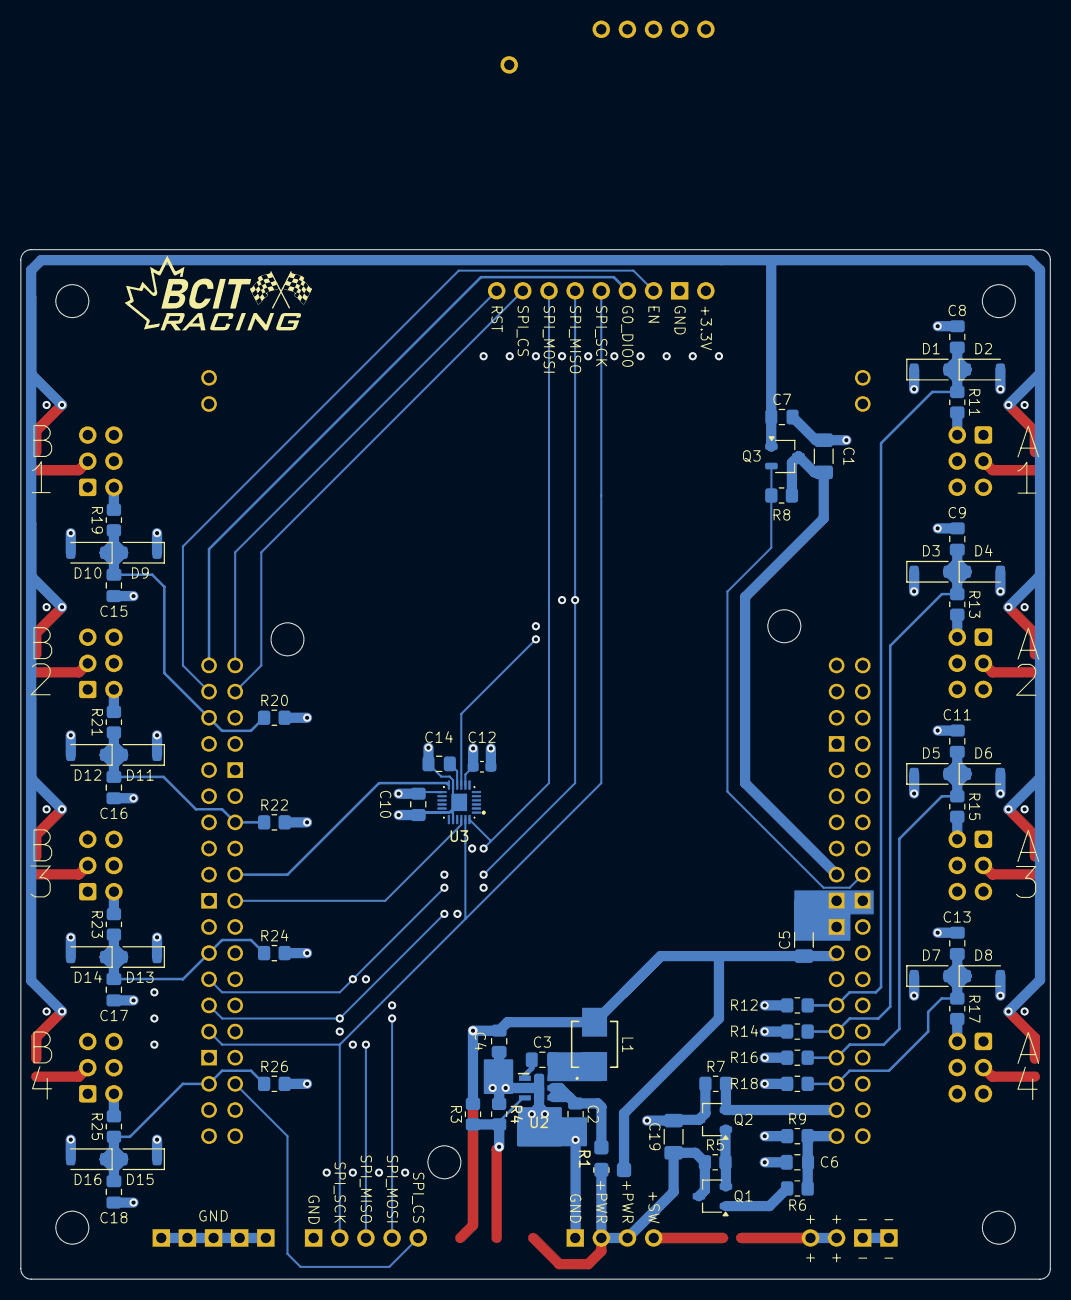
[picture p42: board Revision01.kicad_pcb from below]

Board: 4 copper layers, 100.0 x 100.0 mm, 95 parts (65 on the bottom side), 52 nets.

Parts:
C1, C19: 22uF ±10%; C_1206_3216Metric_Pad1.33x1.80mm_HandSolder
C2, C4: 1uF, X7R; C_0805_2012Metric_Pad1.18x1.45mm_HandSolder
C3: 0.1µF, X7R; C_0805_2012Metric_Pad1.18x1.45mm_HandSolder
C5: 10uF, X7R; C_1206_3216Metric_Pad1.33x1.80mm_HandSolder
C6, C7, C8, C9, C11, C13, C15, C16, C17, C18: 0.1uF ±10%; C_0805_2012Metric_Pad1.18x1.45mm_HandSolder
C10, C14: 0.1µF ±10%, Ceramic, X7R, >2V; C_0805_2012Metric_Pad1.18x1.45mm_HandSolder
C12: 10nF ±10%, Ceramic, X7R, >4V; C_0603_1608Metric_Pad1.08x0.95mm_HandSolder
D1, D2, D3, D4, D5, D6, D7, D8, D9, D10, D11, D12, D13, D14, D15, D16: D_Zener_Small; D_SOD-123
F1: FAST-BLOW 375mA 32V 0.45Ω; Fuse_0603_1608Metric_Pad1.05x0.95mm_HandSolder
F2, F3, F4, F5, F6, F7, F8, F9: 70mA 5s Fusing, 7.5 Ohms; Fuse_0603_1608Metric_Pad1.05x0.95mm_HandSolder
H1, H2, H3, H4: MountingHole; MountingHole_3.2mm_M3
J3: Conn_01x04; BatterySwitch_PinHeader_1x04_P2.54mm_Vertical
J4: Conn_01x05; SPIExtra_PinHeader_1x05_P2.54mm_Vertical
J5: Conn_01x05; GND_PinHeader_1x05_P2.54mm_Vertical
J6, J7, J8, J9, J10, J11, J12, J13: IDC 6Pin Male Header; AdamTech_BHR-06-VUA
J20: Conn_01x04; Battery_PinHeader_1x04_P2.54mm_Vertical
L1: 150uH; LQH44PH151MPRL_IND_LQH44PN_PR_MUR-M
Q1, Q3: PMOS; TSOT-23
Q2: NMOS; TSOT-23
R1: 0; ZeroOhmSwitch_R_0805_2012Metric_Pad1.20x1.40mm_HandSolder
R3: 76.8K+- 1%, ±100ppm/°C; R_0805_2012Metric_Pad1.20x1.40mm_HandSolder
R4: 10K +-1%, ±100ppm/°C; R_0805_2012Metric_Pad1.20x1.40mm_HandSolder
R5, R7, R8: 10K ±1%; R_0805_2012Metric_Pad1.20x1.40mm_HandSolder
R6: 15K ±1%; R_0805_2012Metric_Pad1.20x1.40mm_HandSolder
R9: 5K ±1%; R_0805_2012Metric_Pad1.20x1.40mm_HandSolder
R11, R13, R15, R17, R19, R21, R23, R25: 150 ±1%; R_0805_2012Metric_Pad1.20x1.40mm_HandSolder
R12, R14, R16, R18, R20, R22, R24, R26: 1M ±1%; R_0805_2012Metric_Pad1.20x1.40mm_HandSolder
TP1, TP2, TP4: TestPoint; TestPoint_Pad_D1.5mm
U1: NUCLEO-L476RG; MODULE_NUCLEO-L476RG
U2: LMR51603XFDBVR; LMR51603XFDBVR_DBV0006A-MFG-IPC_C
U3: MPU-6500; MPU-6500_QFN40P300X300X95-25N
U4: Adafruit 3070; Adafruit3070

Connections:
+3.3V: C10.1, C12.1, D1.1 (K), D3.1 (K), D5.1 (K), D7.1 (K), D9.1 (K), D11.1 (K), D13.1 (K), D15.1 (K), U1.CN7_5 (VDD), U1.CN7_16 (+3V3), U3.8 (VDDIO), U3.13 (VDD), U4.1 (VIN)
+5V: C1.1, Q3.3 (S), R8.2, U1.CN7_18 (+5V)
+VBattery: C19.1, J3.2, J3.3, Q1.3 (S), R1.1, R5.2, TP1.1
+VBattery_or_7V: C4.1, C5.1, L1.2, R1.3, R3.2, TP4.1, U1.CN7_24 (VIN)
/AIn_BatteryV: C6.1, R6.1, R9.2, U1.CN7_38 (PC0/ADC123_IN1/LPUART1_RX/LPTIM2_IN1)
/AIn_StrainV_1: C8.1, D1.2 (A), D2.1 (K), R11.1, R12.1, U1.CN7_28 (PA0/ADC12_IN5/USART2_CTS/UART4_TX/TIM2_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)
/AIn_StrainV_2: C9.1, D3.2 (A), D4.1 (K), R13.1, R14.1, U1.CN7_30 (PA1/ADC12_IN6/USART2_RTS_DE/UART4_RX/TI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)
/AIn_StrainV_3: C11.1, D5.2 (A), D6.1 (K), R15.1, R16.1, U1.CN7_32 (PA4/ADC12_IN9/DAC1_OUT1/SPI1_NSS/SPI3_N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)
/AIn_StrainV_4: C13.1, D7.2 (A), D8.1 (K), R17.1, R18.1, U1.CN7_34 (PB0/ADC12_IN15/USART3_CK)
/AIn_StrainV_5: C15.1, D9.2 (A), D10.1 (K), R19.1, R20.1, U1.CN10_6 (PC5/ADC12_IN14/USART3_RX)
/AIn_StrainV_6: C16.1, D11.2 (A), D12.1 (K), R21.1, R22.1, U1.CN10_13 (PA6/ADC12_IN11/SPI1_MISO/USART3_CTS/TIM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)
/AIn_StrainV_7: C17.1, D13.2 (A), D14.1 (K), R23.1, R24.1, U1.CN10_24 (PB1/ADC12_IN16/USART3_RTS_DE/LPTIM2_IN1)
/AIn_StrainV_8: C18.1, D15.2 (A), D16.1 (K), R25.1, R26.1, U1.CN10_34 (PC4/ADC12_IN13/USART3_TX)
/BuckFB: R3.1, R4.2, TP2.1, U2.3 (FB)
/BuckSW: C3.2, L1.1, U2.6 (SW)
/GPIO_ANT_Enable: U1.CN10_4 (PC6), U4.3 (EN)
/GPIO_ANT_Reset: U1.CN10_1 (PC9/TIM8_BKIN2_COMP1), U4.9 (RST)
/GPIO_ANT_SPI_CS: U1.CN10_3 (PB8/CAN1_RX/TIM16_CH1), U4.8 (CS)
/GPIO_BatteryV_Enable: Q2.2 (G), R7.2, U1.CN7_36 (PC1/ADC123_IN2/LPUART1_TX)
/GPIO_Extra_SPI_CS: J4.5, U1.CN10_33 (PA10/USART1_RX/TIM17_BKIN)
/GPInterruptPB6_MPU: U1.CN10_17 (PB6/USART1_TX/TIM16_CH1N), U3.12 (INT)
/GPInterruptPC8_ANT_DIO0: U1.CN10_2 (PC8), U4.4 (G0_DIO0)
/SPI2_MISO: J4.3, U1.CN10_28 (PB14/SPI2_MISO/USART3_RTS_DE/TIM15_CH1), U3.9 (AD0/SDO), U4.6 (MISO)
/SPI2_MOSI: J4.4, U1.CN10_26 (PB15/RTC_REFIN/SPI2_MOSI/TIM15_CH2), U3.24 (SDA/SDI), U4.7 (MOSI)
/SPI2_SCK: J4.2, U1.CN10_30 (PB13/SPI2_SCK/USART3_CTS/LPUART1_CTS/TI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), U3.23 (SCL/SCLK), U4.5 (SCK)
/~GPIO_MPU_SPI_CS: U1.CN10_19 (PC7), U3.22 (nCS)
/~GPIO_StrainV_Enable_5VTolerant: Q3.2 (G), R8.1, U1.CN7_17 (PA15/JTDI/SPI1_NSS/SPI3_NSS/UART4_RTS_DE)
GND: C1.2, C2.2, C4.2, C5.2, C6.2, C7.2, C8.2, C9.2, C10.2, C11.2, C12.2, C13.2, C14.1, C15.2, C16.2, C17.2, C18.2, C19.2, D2.2 (A), D4.2 (A), D6.2 (A), D8.2 (A), D10.2 (A), D12.2 (A), D14.2 (A), D16.2 (A), J3.1, J4.1, J5.1, J5.2, J5.3, J5.4, J5.5, J6.1, J7.1, J8.1, J9.1, J10.1, J11.1, J12.1, J13.1, J20.1, J20.2, Q2.3 (S), R4.1, R7.1, R9.1, R12.2, R14.2, R16.2, R18.2, R20.2, R22.2, R24.2, R26.2, U1.CN7_8 (GND_CN7_8), U1.CN7_19 (GND_CN7_19), U1.CN7_20 (GND_CN7_20), U1.CN7_22 (GND_CN7_22), U1.CN10_9 (GND_CN10_9), U1.CN10_20 (GND_CN10_20), U1.CN10_32 (AGND), U2.2 (GND), U3.11 (FSYNC_or_GND), U3.18 (GND), U3.20 (RESV_GND), U3.25 (ThermalPad_typically_GND), U4.2 (GND)
unnamed: F1.2, J3.4
unnamed: J6.2, R11.2
unnamed: F2.2, J6.3
unnamed: J7.2, R13.2
unnamed: F3.2, J7.3
unnamed: J8.2, R15.2
unnamed: F4.2, J8.3
unnamed: J9.2, R17.2
unnamed: F5.2, J9.3
unnamed: J10.2, R19.2
unnamed: F6.2, J10.3
unnamed: J11.2, R21.2
unnamed: F7.2, J11.3
unnamed: J12.2, R23.2
unnamed: F8.2, J12.3
unnamed: J13.2, R25.2
unnamed: F9.2, J13.3
unnamed: F1.1, J20.3, J20.4
unnamed: Q1.1 (D), R6.2
unnamed: Q1.2 (G), Q2.1 (D), R5.1
unnamed: C7.1, F2.1, F3.1, F4.1, F5.1, F6.1, F7.1, F8.1, F9.1, Q3.1 (D)
unnamed: C3.1, U2.1 (CB)
unnamed: C2.1, R1.2, U2.4 (EN), U2.5 (VIN)
unnamed: C14.2, U3.10 (REGOUT)

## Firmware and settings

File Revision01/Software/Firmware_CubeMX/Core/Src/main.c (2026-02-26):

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
/* Includes ------------------------------------------------------------------*/
#include "main.h"
#include "Common/Protocol.h"

/* USER CODE BEGIN Includes */
#include <stdint.h>
#include <stdbool.h>
#include <stdlib.h>
#include <string.h>
/* USER CODE END Includes */

SPI_HandleTypeDef hspi2;

TIM_HandleTypeDef htim17;

UART_HandleTypeDef huart2;

void SystemClock_Config(void);
static void MX_GPIO_Init(void);
static void MX_SPI2_Init(void);
static void MX_USART2_UART_Init(void);
static void MX_TIM17_Init(void);
/* USER CODE BEGIN 0 */
void HAL_TIM_PeriodElapsedCallback(TIM_HandleTypeDef *htim)
{
    /* Check which timer triggered this callback */
    if (htim->Instance == TIM17) {
        // read
    }
}
/* USER CODE END 0 */

/**
  * @brief  The application entry point.
  * @retval int
  */
int main(void)
{

  /* MCU Configuration--------------------------------------------------------*/

  /* Reset of all peripherals, Initializes the Flash interface and the Systick. */
  HAL_Init();

  /* Configure the system clock */
  SystemClock_Config();

  /* Initialize all configured peripherals */
  MX_GPIO_Init();
  MX_SPI2_Init();
  MX_USART2_UART_Init();
  MX_TIM17_Init();
  /* USER CODE BEGIN 2 */
	{
		const char msg[] = "Hello World from STM32!\r\n";
		HAL_UART_Transmit(&huart2, (const uint8_t*)msg, (sizeof(msg) - 1), 100);
	}

	HAL_TIM_Base_Start_IT(&htim17);
  /* USER CODE END 2 */

  /* Infinite loop */
  /* USER CODE BEGIN WHILE */
	bool blue_pb_down_now = false;
	bool blue_pb_down_was = false;

	int loop_n = 0;
	char number_str[32 + 1] = { 0 };
	while (1) {
    /* USER CODE END WHILE */

    /* USER CODE BEGIN 3 */
		blue_pb_down_now = (GPIO_PIN_RESET == HAL_GPIO_ReadPin(BluePB_Down_N_GPIO_Port, BluePB_Down_N_Pin));
		if (!blue_pb_down_was && blue_pb_down_now) {
			// HAL_GPIO_TogglePin(GPIO_LED2_GPIO_Port, GPIO_LED2_Pin);

			HAL_GPIO_TogglePin(GPIO_StrainV_Enable_5VTolerant_N_GPIO_Port, GPIO_StrainV_Enable_5VTolerant_N_Pin);
		}
		blue_pb_down_was = blue_pb_down_now;
		// HAL_Delay(50);

		++loop_n;
		itoa(loop_n, number_str, 10);
		HAL_UART_Transmit(&huart2, (const uint8_t*)number_str, (1 + strlen(number_str)), 100);
		HAL_Delay(1000);
	}
  /* USER CODE END 3 */
}

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


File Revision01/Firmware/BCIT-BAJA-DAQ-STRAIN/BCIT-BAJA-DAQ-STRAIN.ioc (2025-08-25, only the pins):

Mcu.UserName=STM32L476RGTx
PA0.GPIO_Label=AIn_StrainV_1
PA0.Signal=ADCx_IN5
PA1.GPIO_Label=AIn_StrainV_2
PA1.Signal=ADCx_IN6
PA10.GPIO_Label=GPIO_Extra_SPI_CS_N
PA10.Signal=GPIO_Output
PA2.GPIO_Label=USART_TX
PA2.Signal=USART2_TX
PA3.GPIO_Label=USART_RX
PA3.Signal=USART2_RX
PA4.GPIO_Label=AIn_StrainV_3
PA4.Signal=ADCx_IN9
PA5.GPIO_Label=LD2 [green Led]
PA5.Signal=GPIO_Output
PA6.GPIO_Label=AIn_StrainV_6
PA6.Signal=ADCx_IN11
PB0.GPIO_Label=AIn_StrainV_4
PB0.Signal=ADCx_IN15
PB1.GPIO_Label=AIn_StrainV_7
PB1.Signal=ADCx_IN16
PB13.Signal=SPI2_SCK
PB14.Signal=SPI2_MISO
PB15.Signal=SPI2_MOSI
PB6.GPIO_Label=GPInterruptPB6_MPU
PB6.Signal=GPXTI6
PB8.GPIO_Label=GPIO_ANT_SPI_CS_N
PB8.Signal=GPIO_Output
PC0.GPIO_Label=AIn_BatteryV
PC0.Signal=GPIO_Analog
PC1.GPIO_Label=GPIO_BatteryV_Enable
PC1.Signal=GPIO_Analog
PC13.GPIO_Label=B1 [Blue PushButton]
PC13.Signal=GPXTI13
PC4.GPIO_Label=AIn_StrainV_8
PC4.Signal=ADCx_IN13
PC5.GPIO_Label=AIn_StrainV_5
PC5.Signal=ADCx_IN14
PC6.GPIO_Label=GPIO_ANT_Enable
PC6.Signal=GPIO_Output
PC7.GPIO_Label=GPIO_MPU_SPI_CS_N
PC7.Signal=GPIO_Output
PC8.GPIO_Label=GPInterruptPC8_ANT_DIO0
PC8.Signal=GPXTI8
PC9.GPIO_Label=GPIO_ANT_Reset
PC9.Signal=GPIO_Output

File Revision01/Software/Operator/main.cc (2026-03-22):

//

// Feb 8
// x 30 minutes Get the assertion handler for Windows working
// x 30 minutes Get Mutexes, Atomics, Event queues

// Feb 9
// - 30 minutes Basic packet definition(fake "1khz" data in windows written to.xlsx)
// - 30 minutes Basic UI(just use a single line printf() fflush(stdout) with summary statistics I guess)
// - Stretch Goal : Opening up the serial port and moving the fake data generation to the STM32

// integrate a nice terminal command library like https://github.com/jart/bestline/tree/master
// Audit.h, Basic.h, version.h, etc, all boilerplate
// write assertions (assure, tru) for STM32.
// then define Protocol.h for a packet containing 10kbps 1khz plain-old-data
// integrate the log.h function with threads / message queues (probably requires it tbh for separating logging & input & file writing anyway)
// 
//

// low priority todos
// fix: >LINK : warning LNK4098: defaultlib 'MSVCRT' conflicts with use of other libs; use /NODEFAULTLIB:library 

//
// scan for serial ports
// open serial port
// initiate contact
// use libxlsxwriter to log data
//

#include "PCH.h"

#include "Version.h"

#include "Audit.h"

#define Protocol_Implmentation
#include "Protocol.h"

#define StateMachine_Implementation
#include "StateMachine.h"

#include "Y.h"
#include "Y_EventMM.h"
#include "Y_PoolFairMM.h"
#include "Y_PoolFrugalMM.h"
#include "Y_QueueMM.h"
#include "Y_QueueSS.h"
#include "Y_RWLockMM.h"

#include "OS_AddressEvent.h"
#include "OS_Signal.h"

#include "LogService.h"
#include "DataService.h"
#include "IOService.h"
#include "LogService.h"
#include "DeviceService.h"

int main()
{
	printf(Version_StringLiteral() "\n"); 
	fflush(stdout);

	LogService log;
	IOService io;
	DeviceService device;

	if(!Test_True(LogService_Create(&log))) { return __LINE__; }
	if(!Test_True(IOService_Create(&io))) { return __LINE__; }
	if(!Test_True(DeviceService_Create(&device))) { return __LINE__; }

	// StateMachine_Demo();
	// Audit_Demo();
	IOService_Demo(&log);

	Defer(LogService_Destroy(&log));
	Defer(IOService_Destroy(&io));
	Defer(DeviceService_Destroy(&device));

	LogService_Begin(&log);
	IOService_Begin(&io, &log);
	DeviceService_Begin(&device, &log/*, &File*/);

	Defer(
		DeviceService_SignalEnd(&device);
		DeviceService_WaitForEnd(&device);

		IOService_SignalEnd(&io);
		IOService_WaitForEnd(&io);

		LogService_SignalEnd(&log);
		LogService_WaitForEnd(&log);
	);

	bool run = true;
	while(run) {
		if(_kbhit()) {
			const char ch = _getch();
			if(ch == 27) {
				run = false;
			}
		}

		Sleep(10);
	}

	return 0;
}

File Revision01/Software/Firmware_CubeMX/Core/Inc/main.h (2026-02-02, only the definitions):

#define BluePB_Down_N_Pin GPIO_PIN_13
#define BluePB_Down_N_GPIO_Port GPIOC
#define AIn_BatteryV_Pin GPIO_PIN_0
#define AIn_BatteryV_GPIO_Port GPIOC
#define AIn_StrainV_1_Pin GPIO_PIN_0
#define AIn_StrainV_1_GPIO_Port GPIOA
#define AIn_StrainV_2_Pin GPIO_PIN_1
#define AIn_StrainV_2_GPIO_Port GPIOA
#define AIn_StrainV_3_Pin GPIO_PIN_4
#define AIn_StrainV_3_GPIO_Port GPIOA
#define GPIO_LED2_Pin GPIO_PIN_5
#define GPIO_LED2_GPIO_Port GPIOA
#define AIn_StrainV_6_Pin GPIO_PIN_6
#define AIn_StrainV_6_GPIO_Port GPIOA
#define AIn_StrainV_8_Pin GPIO_PIN_4
#define AIn_StrainV_8_GPIO_Port GPIOC
#define AIn_StrainV_5_Pin GPIO_PIN_5
#define AIn_StrainV_5_GPIO_Port GPIOC
#define AIn_StrainV_4_Pin GPIO_PIN_0
#define AIn_StrainV_4_GPIO_Port GPIOB
#define AIn_StrainV_7_Pin GPIO_PIN_1
#define AIn_StrainV_7_GPIO_Port GPIOB
#define GPIO_ANT_Enable_Pin GPIO_PIN_6
#define GPIO_ANT_Enable_GPIO_Port GPIOC
#define GPIO_MPU_SPI_CS_N_Pin GPIO_PIN_7
#define GPIO_MPU_SPI_CS_N_GPIO_Port GPIOC
#define GPInterruptPC8_ANT_DIO0_Pin GPIO_PIN_8
#define GPInterruptPC8_ANT_DIO0_GPIO_Port GPIOC
#define GPIO_ANT_Reset_Pin GPIO_PIN_9
#define GPIO_ANT_Reset_GPIO_Port GPIOC
#define GPIO_Extra_SPI_CS_Pin GPIO_PIN_10
#define GPIO_Extra_SPI_CS_GPIO_Port GPIOA
#define GPIO_StrainV_Enable_5VTolerant_N_Pin GPIO_PIN_15
#define GPIO_StrainV_Enable_5VTolerant_N_GPIO_Port GPIOA
#define GPInterruptPB6_MPU_Pin GPIO_PIN_6
#define GPInterruptPB6_MPU_GPIO_Port GPIOB
#define GPIO_ANT_SPI_CS_Pin GPIO_PIN_8
#define GPIO_ANT_SPI_CS_GPIO_Port GPIOB

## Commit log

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2025-03-01 idea of how strain gauge interacts with MCU added. Not enough data to perform calculations
    [strainGaugeBCIT_BAJA.kicad_sch]
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2025-03-11 ALL BOM components have been added with manufacturing part nunmber, alongside distributor link
    [BLE_HDWR_DESIGN.csv, bajaSensorPCB.csv, peripherals.kicad_sch]
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2025-03-12 wired, and selected capacitors. Not sure if they are correct as there was nothing in datasheet for it
    [peripherals.kicad_sch, power-supply.kicad_sch]
2025-03-12 gyroscope components wired and added. Pullup resistors may conflict with the other 3.3K pullup
    [ICM-45605.step, LGA14_2P5X3X0P91_IVS.step, peripherals.kicad_sch]
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2025-03-16 . Added NUCLEO reference schematics . Cleaned, renamed schematic pins for clarity . Fixed PMOS polarity bug . Added PMOS for switching StrainV . Added capacitors to AIN, StrainV . Cleaned git reposit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
    [Connectors.SchDoc, Connectors.kicad_sch, MB1136.PcbDoc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]
2025-03-16 Both mosfet will not be added into circuit. Both IMU and ANTENNA have sleep mode, which is in the micro to milliamp current usage range. Add in capacitor will optimize the system slighty, however the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
    Capacitor. Placement of capacitor is not accross differential. But we need 1 cap for each AIN, in addition to this, our switching frequency
    will be varied significantly due to our battery range. This is very complicated stuff to size for. So in terms of time, it may be best to not add this in.
    [Top.kicad_sch, pcb-stm32wl_bajaSensors.kicad_sch, peripherals.kicad_sch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]
2025-03-16 Both mosfet will not be added into circuit. Both IMU and ANTENNA have sleep mode, which is in the micro to milliamp current usage range. Add in capacitor will optimize the system slighty, however the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
    to size for capcitor, we need to know oscillations of buck converter(which is complicated) and is already filtered at output of buck converter. So, I will avoid adding in this.
    [pcb-stm32wl_bajaSensors.kicad_sch]
2025-03-18 . Re-imported NUCLEO_L476RG/BoardDesign/* files using KiCad 9.0.0 one at a time (to avoid a bug evident in misconnections in MCU_64), copied the schematic contents into local kicad_sch files with the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
    [Connectors.kicad_sch, MCU_64.kicad_sch, NUCLEO-L476RG_Connectors.kicad_sch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]
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2025-03-19 added colour scheme for notes. Parry: Orange, Daniel: Green
    Did PMOS calculation check.
    Results: Current mosfets unable to switch 3.3V load if we are using them.
    Calculations can be found in the Applications sheet
    [Revision01.kicad_sch, Revision01_Application.kicad_sch]
2025-03-20 redid mosfet calculations, 3.3V switching load should be fine calculations in application sheet
    [Revision01.kicad_pcb, Revision01_Application.kicad_sch]
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2025-03-22 Mainly verified and fixed peripheral component selection MOSFET-WIREOUT - DONE ANTENNA WIRE-OUT - DONE ADC WIRE-OUT - DONE - found error in ADC wireout, EP was left unconnected - notes on pins I foun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
    CHECK COMPONENT SELECTION ON
    MOSFET - Done
    Need to pick 100K component and 33K components - Done
    ADC - Done
    ANTENNA - Done
    IMU - done
    ADD POWER SWITCH WITH INTEGRATED LED <--- finished
    ADD SERIES AND PULL-UP RESISTORS TO SPI-BUS <--- finished
    Picked power switch with integrated LED
    Picked 10K SPI pullups, and 50Ohm series resistors
    [NUCLEO-L476RG_Connectors.kicad_sch, NUCLEO-L476RG_MCU_64.kicad_sch, NUCLEO-L476RG_Top.kicad_sch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]
2025-03-22 . Added local pin labels, ground, and VIN connections for Controller headers. Digital side TODO
    [NUCLEO-L476RG_Connectors.kicad_sch, NUCLEO-L476RG_MCU_64.kicad_sch, NUCLEO-L476RG_Top.kicad_sch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]
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2025-03-23 . Fixed MCU sheet pins neglecting Button1, Button2, and LED2.
    [Revision01.kicad_sch, Revision01_Controller.kicad_sch]
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2025-03-23 footprint added for nucleo board
    To do before PCB LAYOUT
    clean up schematic
    wire-accross sheets
    Improve annotation ordering
    Perform ERC check
    Ensure all components have footprints
    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
    [Revision01.kicad_sch]
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2025-03-25 neated up the circuit - done wire-accross sheets - done Ensure all components have footprints - done Create net classes - DONE POWER GND SPI GPIO
    Add in new components into BOM
    - Power switch, exclude from BOM - DONE - added component to switch. Not sure how to get it to work
    - Add in the resistors in parallel and series. for SPI busses - Done(PENDING whether to take series resistors out)
    [NUCLEO-L476RG_Connectors.kicad_sch, NUCLEO-L476RG_MCU_64.kicad_sch, NUCLEO-L476RG_Top.kicad_sch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]
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2025-03-27 CREATE STM32CUBEIDE file to verify all ports Check over CONTROLLER SHEET Improve annotation ordering Move testpoints out of controller sheet
    Still performering ERC check
    [NUCLEO-L476RG_Connectors.kicad_sch, NUCLEO-L476RG_MCU_64.kicad_sch, NUCLEO-L476RG_Top.kicad_sch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]
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2025-03-28 Revert "Added new LDO to fit into new battery range."
    This reverts commit 21f4e87803df2792b52a778a93d7df1213cd7c9c.
2025-03-28 Added new LDO to fit into battery range that feeds into MCU, make sure to remove power jumper wire before connecting. Completed ERC check
    Still have to put on footprints for some components when doing PCB layout
    [Revision01.kicad_sch, Revision01_Application.kicad_sch, Revision01_Controller.kicad_sch]
2025-03-28 missed connection for 5V to buck convertor on MCU
    [Revision01_Controller.kicad_sch]
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2025-03-31 added netclasses again changed power to be globally used strain gauges symbol created and added to schematic
    [NCP1117LPST50T3G.step, Revision01.kicad_sch, Revision01_Application.kicad_sch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]
2025-04-09 added 0ohm resistor to power STRAIN GAUGE. Need to re-read ADC to ensure reference is able to read negative voltage, as well as is capable of reading strain gauge
    [Revision01.kicad_sch, Revision01_Application.kicad_sch]
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2025-04-26 wired REFIN-, REFIN+ wired internal lowside ADC PS Changed VCC_STRAIN_GAUGE from 5V -> 3.3V to ensure the measured voltages are within 0-3.3V
    [Revision01_Application.kicad_sch]
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2025-04-27 added new battery measurement circuit which uses load switches onto schematic and changed headers to screw terminals
    [Revision01.kicad_sch, Revision01_Application.kicad_sch]
2025-04-30 Reworked Controller sheet to nucleo L476RG
    [Revision01.kicad_sch, Revision01_Application.kicad_sch, Revision01_Controller.kicad_sch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]
2025-04-30 ADDED 25pF to STRAIN GAUGES to remove noise ADDED FOOTPRINTS TO COMPONENTS Changed PS back to external-highside switch as internal mosfet current rating is too low pull-up for PMOS strainV_enable add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
    [Revision01.kicad_pcb, Revision01.kicad_sch, Revision01_Application.kicad_sch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]
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2025-05-03 feat(pcb layout)- grouped components by function in general area they will be placed in
    [Revision01.kicad_pcb, Revision01_Application.kicad_sch]
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2025-05-08 fixed some ERC errors related to JUMPERS
    [Revision01.kicad_pcb, Revision01.kicad_sch]
2025-05-09 created rainbows! fixed some wiring errors Began component layout( capacitors are huge compared to adc which is only part not layed out) Created board stackup thickness, materials, ect Defined minimu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
    [Revision01.kicad_pcb, Revision01.kicad_sch, Revision01_Application.kicad_sch]
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2025-05-14 some feedback implemented, MISO/MOSI SIWTCHED, GPIO_USB_5V FIXED, COMMENTS REGARDING ALTERNATIVE ADC's, and PCB CONNECTED TO EXTERNAL GND added
    [Revision01.kicad_pcb, Revision01.kicad_sch, Revision01_Application.kicad_sch]
2025-05-16 Implemented new more reliable design utilizing instrumentation amplifiers
    Changed RESISTORS for new Power requirements
    Added prototype features of breathing cube to test out.
    Removed MCU sheet, as moving pins around was getting too messy
    Picked out Instrumentation OP-AMP, INA331 or INA2331
    [691137710003.step, DSD0008B.stp, OSFW4BS8C1A.step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]
2025-05-16 Finished up small things(on schematic layout)
    -Connector pins switched such that GND is pin 1
    -used KICAD feature to indicate ACTIVE LOW
    -polyFuse added to each StrainGauge
    -Added Grounded Mounting holes connects to external GND(outside of PCB)
    [Revision01.kicad_sch, Revision01_Application.kicad_sch]
2025-05-17 I believe I have finished schematic
    -Calculated RC circuit with cutoff at 10KHz for ADC
    - Stimulated OP-AMP circuit with strainGauge
    [Revision01.kicad_pcb, Revision01.kicad_sch, Revision01_Application.kicad_sch]
2025-05-19 schematic wiring, and LT-SPICE simulations on strain gauge - Added buffer with offset at 1.66V to instrumentation amplifier to ensure -20-20mv range can be read - Added caps to Instrumentation Amplif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
    [BOM1.csv, Revision01.kicad_pcb, Revision01.kicad_sch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]
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2025-05-22 Schematic small details, and beginning wiring
    Placed capacitors( in correct polarity)
    Branch fuses should be put on the branches(sensor Amplifiers) - as they protect branches
    Added Main fuse(protecting main circuit - from connector)
    Changed all component sizes back to 0805 atleast
    Started PCB WIRING
    [Revision01.kicad_pcb, Revision01.kicad_sch, Revision01_Application.kicad_sch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]
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2025-05-29 stimulated over/undervoltage protection and started correcting error
    [Revision01.kicad_pcb, Revision01.kicad_sch, Revision01_Application.kicad_sch]
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2025-06-16 attempting to fix software bug
    [Revision01_Application.kicad_sch]
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2025-06-24 PART B- size reduced to enhance mechanical stability, PART A - changed antenna due to being out of stock
    [IND_LQH44PN_PR_MUR.step, Revision01-Parry.kicad_sch, Revision01.kicad_pcb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]
2025-06-25 fixed antenna footprint issue, moved primary fuse upstream before switch, reduced number of 0 ohm resistors needed for switching between PS
    [Revision01.kicad_pcb, Revision01.kicad_sch, Revision01_Application.kicad_sch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]
2025-06-25 antenna connections are flipped, fixed
    [Revision01.kicad_pcb, Revision01.kicad_sch, Revision01_Application.kicad_sch]
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2025-06-28 review 2 implemented
    - Made mounting holes symmetrical
    - Buck enable 0 ohm resistor error fixed
    [Revision01-DESKTOP-HRPABPU.kicad_pcb, Revision01.kicad_sch, Revision01_Application-DESKTOP-HRPABPU.kicad_sch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]
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2025-07-05 Fixed minor ERC Errors.
    [Revision01.kicad_sch, Revision01_Application.kicad_sch]
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2025-07-06 Excluded 1 Warning: Symbol 'SW_SPST_LED' doesn't match copy in library 'Switch' Fixed 3 Warnings: Symbol 'R_Small' doesn't match copy in library 'Device'
    [Revision01.kicad_sch]
2025-07-06 ERC Warning Count: 31
    Fixed 1 Warning: Symbol U1: Symbol 'NUCLEO-L476RG' doesn't match copy in library 'NUCLEO-L476RG'
    Fixed 3 Warnings: STM local net label & global net label mismatches:
    "Both +5V and +5V_NUCLEO are attached to the same items; +5V will be used in the netlist"
    [Revision01.kicad_sch]
2025-07-06 ERC Warnings: 21
    - Replaced 8x Strain Gauge JST Connector footprints with 2x3 2.54mm Odd/Event 6-Pin IDC.
    The case connectors are 6 pin (inner) Male -> Female -> Male (outer)
    [Revision01_Application.kicad_sch]
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2025-07-06 ERC Warnings: 7
    . Fixed incorrect AIN_STRAIN_1..8 "Input" setting. They are outputs according to the application module.
    . Reworked strain gauge schematic to flow from left to right, removing unnecessary and error-prone local net names.
    [Revision01.kicad_sch, Revision01_Application.kicad_sch]
2025-07-06 ERC Warnings: 7
    . Reworked Power section to flow from left to right.
    . Separated the Power switch connector from the external SPST + LED component.
    . Changed most NOT POPULATED external flags to Excluded from Simulation only. It gives a nice visual gray without exclusion from BOM.
    [Revision01.kicad_sch, Revision01_Application.kicad_sch]
2025-07-07 Reworked NUCLEO-L476RG schematic symbols to include important pin functions.
    [Revision01.kicad_sch, Revision01_Application.kicad_sch, nucleo_L476RG_pinout_matrix.ods]
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2025-07-07 ERC Warnings: 6
    . Fixed 100uF capacitor upstream of PMOS Switch
    . Fixed MPU-6500 floating pins
    . Fixed STM PA2, PA3 USART2 AIN overlap bug
    . Added ANT_Enable pin
    . Created Adafruit 3070 symbol, added SMA & Antenna component symbols.
    [Revision01.kicad_sch, Revision01_Application.kicad_sch]
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2025-07-08 Normalized Symbol Fields.
    . Populated symbol fields with Detailed Description, Distributor Link, Distributor Part Number, Manufacturer, Manufacturer Part Number, Package / Case
    . Replaced all resistors with Vishay, capacitors with Samsung components.
    . Chose 22uF capacitor for the +5V strain gauge power MOSFET
    [Revision01.kicad_sch, Revision01_Application.kicad_sch]
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2025-07-09 . Changed to 1-shot fast-blow fuses to replace erroneous main PTC fuse, strain fuses. . Added BOM entry for BF350 strain gauges from aliexpress
    [Revision01.kicad_sch, Revision01_Application.kicad_sch]
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2025-07-13 Improved documentation on LTSPICE schematics - Created WORD document containing documentation on all LTSPICE stimulations - Changed strainPower mosfet to NMOS <- subject to change - Redid clamping di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
    Having issues integrating amplifier schematic with clamping diode schematic.
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2025-07-14 - Redo buck converter calculations - Maybe stimulate it. - Choose components for RC mosfet circuit - Verify MOSFET calculations - tried and changed PMOS type - Check fuse selection. Accounting for BU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
    [Revision01.kicad_sch, Revision01_Application.kicad_sch, StrainAmplifierV1.kicad_pcb]
2025-07-16 Documentation files on LTSPICE stimulations, as well as RC FILTER created
    LTSPICE stimulations
    ALL circuits restimulated, documented in test folder
    RC FILTER calculations which filters out a lot of noise concerns.
    [Revision01.kicad_sch, Revision01_Application.kicad_sch, StrainAmplifierV1.kicad_sch]
2025-07-16 some files were missed last commit
    [Revision01_Application.kicad_sch]
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2025-07-28 . Ensured interrupts were not overlapping by renaming PB4_GPIO to PB4_GPInterrupt . Checked PC6 for 5V tolerance (FT) . Fixed ERC errors for unconnected pins.
    [Revision01.kicad_sch, Revision01_Application.kicad_sch]
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2025-07-30 . Added Adamtech male 6 pin IDC connector footprint & 3D Model, revealing critical overlapping problem on fuses. . Added NUCLEO additional plated holes to fit USB debugging GND connections. . Placed 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
    [Revision01.kicad_pcb, Revision01.kicad_sch, Revision01_Application.kicad_sch]
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2025-08-01 . Repositioned antenna close to USB for space considerations . Repositioned connectors, headers, testpoints, buck, switch, etc. . Fixed Adafruit Pad 15 Error . Fixed MPU-6500 missing Pad Warnings/Err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
    [Revision01.kicad_pcb, Revision01.kicad_sch, Revision01_Application.kicad_sch]
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2025-08-04 . Fixed DRC Violations
    [Revision01.kicad_pcb]
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2025-08-05 . Placed vias. . Added bypass capacitor to BatteryV measurement circuit. . Fixed prior git incomplete checkins by adding custom footprints.
    [Revision01.kicad_pcb, Revision01.kicad_sch, Revision01_Application.kicad_sch]
2025-08-07 . Completed KiCad track wiring. DRC Errors: 0 DRC Warnings: 55
    [Revision01.kicad_pcb, Revision01.kicad_sch, Revision01_Application.kicad_sch]
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2025-08-10 . Added ZeroOhmSwitch symbol & footprint for the Buck bypass . Adjusted holes to 5mm offset from edge for clearance from C8, C18 for standoffs . Added back silkscreen for PWR SWITCH headers . Minimiz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
    [21-0137I_T1033-1_MXM.step, 691137710003.step, 691137710004.step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]
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2025-08-13 . Moved R from main board to amplifier board to current limit the INA amplifier in case of cable short to GND . replaced RC filter with 500ohm, 6.8nF, in order to current limit the INA amplifier to 1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
    [Amplifier.kicad_sch, DBV0006A.stp, Hub.kicad_sch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]
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2025-08-16 . Amplifier: Changed 200K / 100K bias divider to 20K / 10K instead of placing a stability capacitor. . Amplifier: Found Mouser.ca components
    [Amplifier.kicad_pcb, Amplifier.kicad_sch]
2025-08-16 . Fixed major BOM bug in Antenna, ordering correct Male Outer, Male Inner Part . Added Mouser column in Hub.
    [Hub.kicad_sch, Hub_Application.kicad_sch]
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2025-08-17 . Made sure amplifier passive silk screen doesn't overlap pads . Added 6xAA battery holder to hub BOM . Exported gerbers, drl files .zip (PCBWay approved)
    [Amplifier-B_Cu.gbl, Amplifier-B_Cu.gbr, Amplifier-B_Mask.gbs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]
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2025-08-19 changes to routing
    -buck converter output capacitors placed at output of inductor
    -output of buck-converter routed over to other layer to further avoid coupling between analog signals
    -1M ohm resistors routed closer to analog signal( so it is less likely to become a victim)
    -initial placement of stitching via's placed. With an average distance of 10mm between them
    [Amplifier.kicad_sch]
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2025-08-20 . Reverted Hardware/ changes to last known good commit f7a44a23fed9aca3ce7036a9f440c4d810a77518
    [Amplifier.kicad_sch, Hub.kicad_sch, Hub_Application.kicad_sch]
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2025-08-29 . Hub & Amp: Changed wiring standard to GND SIG GND GND PWR GND . Hub: Added GND plane to 3.3V . Hub: Moved 1M pulldown resistor . Hub & Amp: Adjusted thermal relief tolerances . Hub: Changed buck co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
    [Amplifier.kicad_pcb, Amplifier.kicad_sch, Hub.kicad_sch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]
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2025-09-04 . Updated QSpice strain gauge schematic to show transient current problem into the microcontroller sink.
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2025-12-15 (hardware Testing) board 1 and 2 have been verified to work: bug is attributed to testing software bug.
    - the bug found was toggling input W1 and W2 on and off with same settings at like 1 Khz results in varying amplitudes, even though the
    settings remain at +-10mV
    [TestingResults.xlsx]
2025-12-15 (hardware Testing) attached strain gauge onto board 1 for basic testing
    - offset voltage is about 1.44V rather than 1.67V
    - bent strain gauge and saw change in voltage
    [TestingResults.xlsx]
2026-01-22 (testing) uploaded loading test on amplifier data - fixed TLV9061-Q1 shutdown pin to be tied to 5V instead of GND
    [Amplifier.kicad_sch, StrainGaugeLoadTests.xlsx]
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2026-02-02 . Tested 500 kbps serial (working) using CoolTerm . Fixed default GPIO settings in CubeMX.
    [Firmware.ioc, main.c]
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2026-02-26 . Fixed a default case fallthrough bug with StateMachine.h, and polished it
2026-03-11 Added an Audit system in order to capture thread local errors like GetLastError()
    [Basic.h]
2026-03-12 Introduced Audit_ReturnIfUntrue, fixed a scope sizing bug in Auditor, slightly integrated the system into DeviceService.cc
2026-03-12 Reworked DeviceService.cc to close and re-open the COM port successfully, despite unplugging and plugging.
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

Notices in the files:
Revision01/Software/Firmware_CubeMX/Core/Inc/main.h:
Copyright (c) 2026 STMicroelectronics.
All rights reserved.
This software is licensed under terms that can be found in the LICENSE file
